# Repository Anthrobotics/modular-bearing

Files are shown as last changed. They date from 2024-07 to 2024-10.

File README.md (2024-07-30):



# modular-bearing
A lightweight, customizable and parametric bearing, manufacturable using 3D printing and CNC machining.

# Description
The modular bearing is designed as an alternative for non-replaceable (or difficult to replace) bearings in robotic joints and actuators. It is customized using an OpenSCAD generator, and can be used in a wide number of designs. It can be swapped out without requiring any tools, depending on how it is integrated into a design.



# Specifications
The following parameters of the modular bearing can be customized:
- Outer diameter (OD)
- Inner diameter (ID)
- Width
- Number of rolling elements
- Diameter of rolling elements
- Spacing of rolling elements in cage
- Tolerances of rolling and sliding surfaces
- Chamfer of rolling elements
- Inner and outer screw hole diameter
- Inner and outer screw hole count
- Edge distance of screw holes
- Optional secondary screw holes



# Testing
Rotation tests have been performed by hand on the modular bearing, demonstrating smooth motion. Testing with the WOLF actuator will be conducted soon.
Test video below (redirects to YouTube):

<div align="center">
      <a href="https://www.youtube.com/watch?v=DmYjyulmFeA">
     Test Video
      </a>
    </div>

# Bill of Materials
You will need the following:

Printed components:
- 1x inner ring
- 1x cage
- 1x outer ring, lower
- 1x outer ring, upper
- rolling elements (number will vary)

COTS components:
The size and quantity of commercial fasteners will vary depending on the configuration of the bearing. The following components are recommended for use with the modular bearing:
- roll pins (to secure the outer ring halves together)
- countersunk bolts, to attach the bearing

Tools:
- 3D printer
- Tweezers (to assist with bearing assembly)
- PTFE lubricant (Super-Lube) for bearing races and rolling elements

# Assembly Guide
## The bearing shown below is configured for the [WOLF actuator](https://github.com/Anthrobotics/wolf-actuator), however, the assembly procedure will apply to any modular bearing.
## Step 1: Place the inner ring inside of the lower half of the outer ring.



## Step 2: Place the cage in between the inner ring and lower half of the outer ring.



## Step 3: Insert the rollers into the cage. Alternate orientation of the rollers as shown below.





## Step 4: Apply PTFE lubricant (Super-Lube) to the rollers. Place the upper half of the outer ring on top of the lower.



## Step 5: Secure the outer ring halves using 6 or 12 M3x10mm roll pins, by inserting them into the secondary holes of the rings.
### Note: It is advised to use the secondary holes to the left or right of the middle one, as that hole will typically be used to secure loads.





# Usage
The modular bearing can be integrated into a number of designs, including:
- robotic joints
- actuators
- motion platforms

# Contribute

Contributions from the community are welcomed! Please send us a message if you are interested in collaborating.

# License

Shield: [][cc-by-sa]

This work is licensed under a
[Creative Commons Attribution-ShareAlike 4.0 International License][cc-by-sa].

[][cc-by-sa]

[cc-by-sa]: http://creativecommons.org/licenses/by-sa/4.0/
[cc-by-sa-image]: https://licensebuttons.net/l/by-sa/4.0/88x31.png
[cc-by-sa-shield]: https://img.shields.io/badge/License-CC%20BY--SA%204.0-lightgrey.svg

# Contact

If you have any questions or need support, please feel free to open an issue or contact us at:

Email: support@anthrobotics.ca

Website: [anthrobotics](https://anthrobotics.ca/)

Twitter: [@anthrobo](https://x.com/Anthrobo)



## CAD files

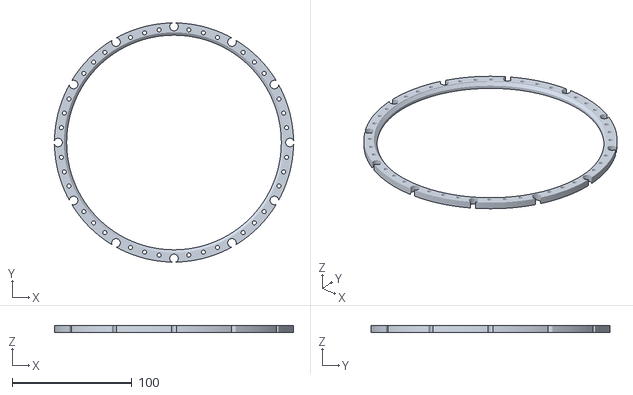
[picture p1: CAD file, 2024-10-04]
CAD/stl/wolf-outer-ring-lower.stl
199.9 x 199.9 x 5.50

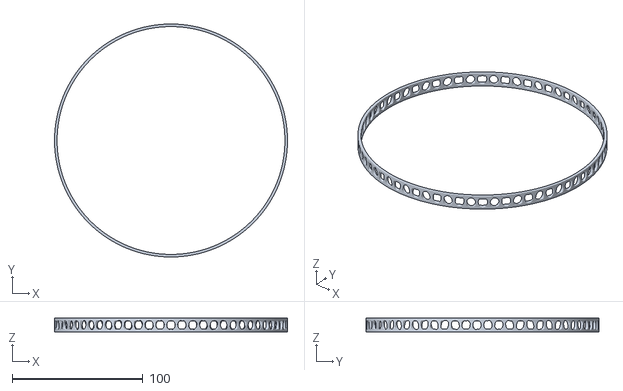
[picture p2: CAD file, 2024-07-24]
CAD/stl/wolf-cage.stl
178.5 x 178.5 x 10.5

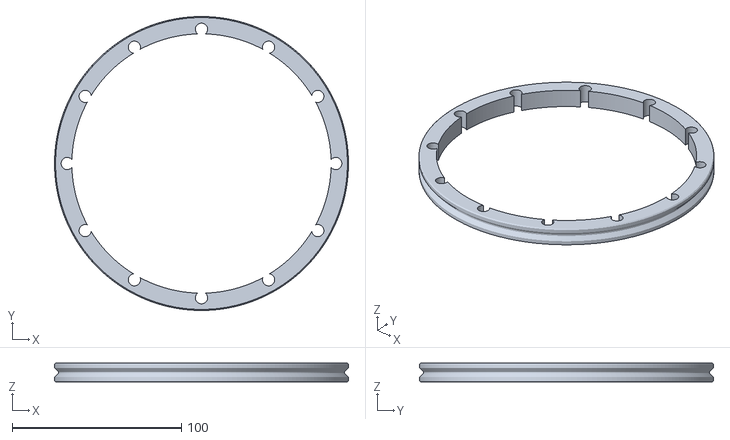
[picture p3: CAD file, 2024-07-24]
CAD/stl/wolf-inner-ring.stl
173.5 x 173.5 x 11.0

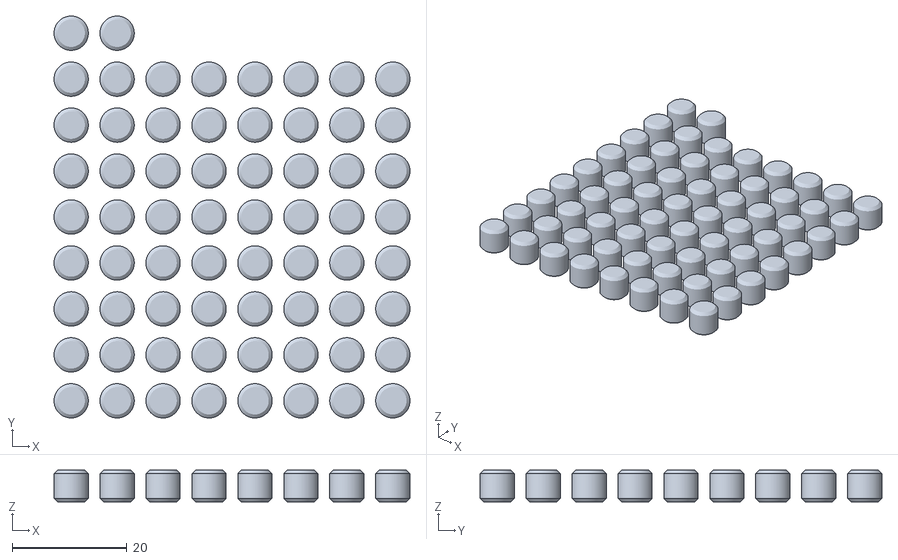
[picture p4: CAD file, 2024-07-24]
CAD/stl/wolf-rollers.stl
62.0 x 70.0 x 5.50

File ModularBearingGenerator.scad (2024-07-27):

/*

MODULAR BEARING GENERATOR

https://github.com/Anthrobotics/modular-bearing

© ANTHROBOTICS 2024
anthrobotics.ca

Developed by Ian Pritchard
github.com/AnthroDev

This work is licensed under a Creative Commons Attribution-ShareAlike 4.0 International License.


*/

/* --USAGE--

Toggle which component you want to see in the viewport. 

 All bearing components can be viewed as an assembled unit using the "overview" option.

 To see a cutaway view of the entire bearing, toggle the "cutaway" option. This can be useful for checking the tolerances of the rollign elements. (enabled by default)
 
 Once the desired viewport options ahev been selected, configure the parameters of the bearing as required.
 
 The default parameters were used to generate the bearings for the WOLF Actuator [v1.1]
 
 */

// VIEWPORT OPTIONS //

// Select visible part(s)

part = "overview"; // [outer_ring_upper:Outer ring upper,outer_ring_lower:Outer ring lower,inner_ring:Inner ring,rollers:Roller,cage:Cage,overview:Overview]

//Toggle cutaway view
cutaway = 1;

// BEARING PARAMETERS

// Outer diameter (mm)
d_outer = 200;

// Bore diameter (mm)
d_bore = 153;

// Width (mm)
width = 11;

// Chamfer size (WxH, mm)
chamfer = 0.6;

// Spacing between rolling surfaces (tolerance)
t_roll = 0.01;

// Spacing between sliding surfaces (tolerance)
t_slide = 0.25; //0.3

// Roller diameter (mm)
// Entering a value of -1 will enable automatic calculation
d_roller = 6; 

// Resolution of circles
fn = 180;

// Screw hole count, outer ring
screw_hole_count_outer = 12;

// Secondary screw hole count, outer ring
screw_hole_count_outer_sec = 24;

//Screw hole count, inner ring
screw_hole_count_inner = 12;

// Screw hole diameter, outer ring (mm)
screw_hole_diam_outer = 7.2;

// Secondary screw hole diameter, outer ring (mm)
screw_hole_diam_outer_sec = 3.4;

// Screw hole diameter, inner ring (mm)
screw_hole_diam_inner = 7.2;

// Distance of screw holes from the edge of the outer ring (mm)
screw_hole_edge_distance_outer = 3;

// Distance of secondary screw holes from edge of the outer ring (mm)
screw_hole_edge_distance_outer_sec = 3;

// Distance of secondary screw holes from edge of the inner ring (mm)
screw_hole_edge_distance_inner = 3;

//Spacing between rolling elements inside the cage (mm)
roll_spacing = 2;

//USED FOR RENDERING//
cube_size = 10; // [1:100]
cylinder_size = 10; // [1:100]
dr_cage_space = 3;


print_part();


module print_part() {
	if (part == "outer_ring_upper") {
		outer_ring_upper(r2=d_outer/2, r1=d_bore/2, d_roller=d_roller, h=width);
	} else if (part == "outer_ring_lower") {
		outer_ring_lower(r2=d_outer/2, r1=d_bore/2, d_roller=d_roller, h=width);
	} else if (part == "inner_ring") {
		translate([0,0,width/2]) inner_ring(r2=d_outer/2, r1=d_bore/2, d_roller=d_roller, h=width);
	} else if (part == "rollers") {
		translate([0,0,(nominal_roller_diam(d_roller, width)-2*t_slide)/2]) 
            print_rollers(r2=d_outer/2, r1=d_bore/2, d_roller=d_roller, h=width);
	} else if (part == "cage") {
		translate([0,0,width/2-t_slide]) cage(r2=d_outer/2, r1=d_bore/2, d_roller=d_roller, h=width);
	} else {
        crossed_roller_bearing(r2=d_outer/2, r1=d_bore/2, d_roller=d_roller, h=width);
	}
}


module crossed_roller_bearing(r2, r1, d_roller, h)
{
    difference() {
        translate([0,0,width/2]) {
            difference() {
                translate([0,0,width/2]) rotate([180,0,0])outer_ring_upper(r2, r1, d_roller, h);
                if(cutaway==1){            
                translate([1000,0,0])cube(2000, center=true);
            }
            }
            translate([0,0,-width/2]) outer_ring_lower(r2, r1, d_roller, h);
            inner_ring(r2, r1, d_roller, h);
        
            dk = nominal_roller_diam(d_roller, h);
            rc = (r2+r1)/2;
            N = number_of_rollers(rc, dk, h);

            for(i = [0 : 1 : N-1])
                rotate([0,0,i*360/N]) translate([0,rc,0]) 
                    rotate([-45+90*(i % 2),0,0]) 
                        roller(nominal_roller_diam(d_roller, width)-2*t_roll, 
                               nominal_roller_diam(d_roller, width)-2*t_slide, 
                               chamfer=chamfer);
            
            cage(r2=d_outer/2, r1=d_bore/2, d_roller=d_roller, h=width);
        }
        if(cutaway==1){
        translate([1000,1000,0])cube(2000, center=true);
    }
}
}


function nominal_roller_diam(d_roller, h) = 
            d_roller <= 0 ? h*9/15 : d_roller;
function number_of_rollers(rc, d_roller, h) = 
            2*floor(3.14159265*rc / (nominal_roller_diam(d_roller, h)+2*t_slide+roll_spacing)+0.5);


module outer_ring_upper(r2, r1, d_roller, h)
{
    translate([0,0,h/2]) difference() {
        outer_ring_half(r2, r1, d_roller, h);
    }
}


module outer_ring_lower(r2, r1, d_roller, h)
{
    translate([0,0,h/2]) difference() {
        outer_ring_half(r2, r1, d_roller, h);
    }
}


module outer_ring_half(r2, r1, d_roller, h)
{
    dk = nominal_roller_diam(d_roller, h);
    rc = (r2+r1)/2;
    r_inside = rc + dr_cage_space/2;
    r_bp1 = rc + dk/2*sqrt(2);
    r_bm1 = rc - dk/2*sqrt(2);

    difference() {
        union() {
            rotate([180,0,0]) 
                difference() {
                    cylinder(r=r2, h=h/2, center=false, $fn=fn);
                    cylinder(r=r_inside, h=h, center=false, $fn=fn);
                    translate([0,0,-r_bp1]) cylinder(r1=2*r_bp1, r2=0, h=2*r_bp1, center=false, $fn=fn);
                }
            
            translate([0,0,-h/8]) difference() {
                cylinder(r=r_bp1+sqrt(0.5)*chamfer,h=h/4, center=true, $fn=fn);
                cylinder(r=r_bp1-sqrt(0.5)*chamfer,h=h, center=true, $fn=fn);
            }
        }
        
        // Chamfer
        cylinder_inside_chamfer_cutout(2*r_inside, h/2, chamfer, 0.5*fn);
        rotate([180,0,0]) cylinder_inside_chamfer_cutout(2*r_inside, h/2, chamfer, 0.5*fn);

        // Screw holes
        M0 = screw_hole_count_outer;
        for(i = [0 : 1 : M0-1])
            rotate([0,0,i*360/M0]) translate([r2-screw_hole_edge_distance_outer,0]) 
                cylinder(d=screw_hole_diam_outer, h=2*h,center=true,$fn=0.25*fn);
                
        // Screw holes, secondary
        M1 = 2* screw_hole_count_outer_sec;
        for(i = [0 : 1 : M1-1])
            rotate([0,0,i*360/M1]) translate([r2-screw_hole_edge_distance_outer_sec,0]) 
                cylinder(d=screw_hole_diam_outer_sec, h=2*h,center=true,$fn=0.25*fn);    
                
    }
}


module inner_ring(r2, r1, d_roller, h)
{
    dk = nominal_roller_diam(d_roller, h);
    rc = (r2+r1)/2;   
    r_outside = rc-dr_cage_space/2;
    r_bp1 = rc + dk/2*sqrt(2);
    r_bm1 = rc - dk/2*sqrt(2);
 
    union() {
        difference() {
            cylinder(r=r_outside, h=h, center=true, $fn=fn);
            cylinder(r=r1, h=2*h, center=true, $fn=fn);
             difference() {
                cylinder(r=rc, h=1.5*h, center=true, $fn=fn);
                translate([0,0,-r_bm1]) cylinder(r1=2*r_bm1, r2=0, h=2*r_bm1, center=false, $fn=fn);
                rotate([180,0,0]) translate([0,0,-r_bm1]) cylinder(r1=2*r_bm1, r2=0, h=2*r_bm1, center=false, $fn=fn);
                difference() {
                    cylinder(r=r_bm1+sqrt(0.5)*chamfer,h=h/4, center=true, $fn=fn);
                    cylinder(r=r_bm1-sqrt(0.5)*chamfer,h=2*h, center=true, $fn=fn);
                }
            }
           
            // Chamfer
            cylinder_chamfer_cutout(2*r_outside, h/2, chamfer, 0.5*fn);
            rotate([180,0,0]) cylinder_chamfer_cutout(2*r_outside, h/2, chamfer, 0.5*fn);

            // Screw holes
            M = screw_hole_count_inner;
            for(i = [0 : 1 : M-1])
                rotate([0,0,i*360/M]) translate([r1+screw_hole_edge_distance_inner -0.27, 0]) 
                    cylinder(d=screw_hole_diam_inner, h=2*h,center=true,$fn=0.25*fn);
        }

    }
}


module roller(d, h, chamfer)
{
    difference() {
        cylinder(d=d, h=h, center=true, $fn=0.5*fn);
        
        // Chamfer
        cylinder_chamfer_cutout(d, h/2, chamfer, 0.5*fn);
        rotate([180,0,0]) cylinder_chamfer_cutout(d, h/2, chamfer, 0.5*fn);
    }
}


module print_rollers(r2, r1, d_roller, h)
{
    dk = nominal_roller_diam(d_roller, h);
    rc = (r2+r1)/2;
    N = number_of_rollers(rc, dk, h);
    echo(d_roller=d_roller, h=h, N=N);
    
    m = floor(sqrt(N)+0.5);

    for(i = [0 : 1 : N-1]) {
        y = floor(i/m);
        x = i  - m*y;
        translate([(dk+roll_spacing)*x, (dk+roll_spacing)*y,0]) 
            roller(nominal_roller_diam(d_roller, width)-2*t_roll, 
                   nominal_roller_diam(d_roller, width)-2*t_slide, 
                   chamfer=chamfer);
    }
}


module cage(r2, r1, d_roller, h)
{
    dk = nominal_roller_diam(d_roller, h);
    rc = (r2+r1)/2;       
    N = number_of_rollers(rc, dk, h);
    echo(required_number_of_rollers=N);
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

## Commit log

2024-07-24 Add files via upload
    Files specific to WOLF V1.1
    [wolf-cage.stl, wolf-inner-ring.stl, wolf-outer-ring-lower.stl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]
2024-07-27 Uploaded OpenSCAD generator
    [ModularBearingGenerator.scad]
2024-07-27 Update ModularBearingGenerator.scad
    License info added
    [ModularBearingGenerator.scad]
2024-07-30 Update README.md
    - added assembly guide,
    - fixed typos
2024-10-04 Updated upper and lower rings for WOLF V1.2
    Changes:
    - The upper and lower rings have been modified to provide more material for securing loads to the WOLF actuator.
    - Only these two files require reprinting for existing bearings on WOLF V1.1 onwards.
    [wolf-outer-ring-lower.stl, wolf-outer-ring-upper.stl]
